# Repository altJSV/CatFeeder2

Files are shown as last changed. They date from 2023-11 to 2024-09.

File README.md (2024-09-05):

# CatFeeder 2
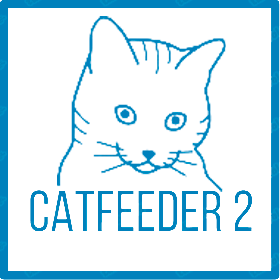
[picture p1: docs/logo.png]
Лого


Полная переработка проекта [CatFeeder](https://github.com/altJSV/CatFeeder) под ESP32.

## Оглавление
* [1. Особенности проекта](#Особенности-проекта)
*  [1.1. Отличия от CatFeeder](#Отличия-от-CatFeeder)
* [2. Сборка проекта](#Сборка-проекта)
*  [2.1. Необходимые компоненты](#Необходимые-компоненты)
*  [2.2. Сборка на макетной плате](#Сборка-на-макетной-плате)
*  [2.3. Сборка основного модуля управления](#Сборка-основного-модуля-управления)
*  [2.4. Подключение шагового двигателя](#Подключение-шагового-двигателя)
*   [2.4.1. Подключение драйвера MX1508](#Подключение-драйвера-MX1508)
*   [2.4.2. Подключение драйвера A4988](#Подключение-драйвера-A4988)
*  [2.5. Подключение весов](#Подключение-весов)
* [3. Прошивка](#Прошивка)
*  [3.1. Сборка из исходников](#Сборка-из-исходников)
*  [3.1.1. Необходимые библиотеки](#Необходимые-библиотеки)
*  [3.1.2. Особенности использования библиотек](#Особенности-использования-библиотек)
*  [3.2. Прошивка бинарных файлов](#Прошивка-бинарных-файлов)
* [4. Сборка-корпуса](#Сборка-корпуса)
* [4.1. Основная часть](#Основная-часть)
*  [4.2. Шнек](#Шнек)
*  [4.3. Миска](#Миска)
*  [4.4. Крышка с бункером для корма](#Крышка-с-бункером-для-корма)
*  [4.5. Регулируемые стойки](#Регулируемые-стойки)
* [5. Особенности использования](#Особенности-использования)
* [5.1. Первый запуск](#Первый-запуск)
*  [5.2. Управление с сенсорного экрана](#Управление-с-сенсорного-экрана)
*  [5.3. Веб интерфейс](#Веб-интерфейс)
*  [5.4. Настройка весов](#Настройка-весов)
*  [5.5. Управление через Telegram](#Управление-через-Telegram)
*  [5.6. Управление по MQTT](#Управление-по-MQTT)

## Особенности проекта
* Цветной TFT экран с сенсорным управлением
* Часы с синхронизацией времени по NTP протоколу
* Отображение температуры и влажности в помещении
* Настройки размера порции и времени кормления с 4 независимыми будильниками
* Точная настройка размера порции с помощью цифровых весов
* Калибровка цифровых весов в зависимости от температуры в помещении
* Проверка наличия корма в бункере и отслеживание забивания подающего лотка
* Уведомления и настройка некоторых параметров в Telegram
* OTA обновление прошивки как через веб интерфейс, так и через Телеграм бота
* Управление по MQTT протколу для интеграции в систему умного дома
* Веб интерфейс
* Сохранение и запись настроек в файлы конфигурации

### Отличия от CatFeeder
* Кормушка построена на базе ESP32, что позволяет существенно расширить ее функционал.
* Для управления используется цветной сенсорный дисплей ILI9341.
* Интерфейс реализован с помощью библиотеки LVGL.
* Все управление и настройки теперь осуществляется с помощью сенсорного экрана, что намного повышает удобство работы.
* Также был полностью переработан веб интерфейс и добавлено управление через телеграмм бота.
* Полностью переписано OTA обновление прошивки
* Работа через MQTT пока изменениям не подвергалась
* Все основные модули распаяны на макетной плате с колодками, для легкой замены.
* Шаговый двигатель теперь используется NEMA 17HS4023. По сравнению с предыдущим вариантом он более компактный и занимает гораздо меньше в корпусе. Мощность у него, конечно поменьше, но со своей задачей вращения шнека он полностью справляется.
* Полностью был переделан корпус. Как мне кажется, он стал более симпатичным и, надеюсь, поможет избавиться от проблемы застревания корма в подающем лотке.
* Также была полностью изменена логика выдачи корма. Теперь это не абстрактные цифры, а вполне конкретный вес в граммах. Для этого в корпус были интегрированы цифровые весы. Это позволяет не только точно отслеживать количество выдаваемого корма, но и своевременно реагировать на различные внештатные ситуации. Например "холостой ход двигателя" из-за застревания или окончания корма. Или же наоборот, подача корма в переполненную миску.

## Сборка проекта

### Необходимые компоненты
Для сборки проекта вам понадобятся следующие компоненты:
* Любая отладочная плата на базе ESP32. Я использовал [ESP32 WROOM 38 PIN](https://aliexpress.ru/item/1005004697343896.html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)
* Драйвер мотора MX1508. Например [такой](https://aliexpress.ru/item/1005001636421978.html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) или [драйвер шагового двигателя A4988](https://www.ozon.ru/product/a4988-stepper-motor-driver-with-ext-board-drayver-shagovogo-dvigatelya-s-platoy-rasshireniya-688838720/)
* [Повышающий преобразователь напряжения MT3608](https://www.ozon.ru/product/povyshayushchiy-preobrazovatel-napryazheniya-dc-dc-gsmin-mt3608-2a-vhod-2-24v-vyhod-5-28v-siniy-799440534/) - только при использовании драйвера A4988
* Шаговый двигатель [NEMA17 17HS4023](https://aliexpress.ru/item/10000232580902.html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)
* Сенсорный дисплей [ILI9341 2.8'](https://aliexpress.ru/item/4000219159401.html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) с разрешением 320x240 и драйвером тача XPT2046
* [Тензодатчик 5кг + драйвер HX711](https://aliexpress.ru/item/33046037411.html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)
* Набор проводов для соединений
* [Макетная плата 50х70 мм](https://aliexpress.ru/item/32945724064.html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)
* [Несколько разъемов hx2.54](https://aliexpress.ru/item/1005001479020815.html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) или похожих для подключения проводов
* [2 безголовых винта M3x2mm](https://aliexpress.ru/item/1005005451331078.html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) 
* [Модуль DHT22](https://aliexpress.ru/item/33037061522.html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)
* Качественный блок питания 5В 3А. Например [такой](https://www.ozon.ru/product/blok-pitaniya-5v-3a-micro-usb-dlya-raspberry-pi-3-i-pi-2-novaya-plata-422415562/) 
* Пластиковый квадратный пищевой контейнер с шириной основания 96 мм. Например [такой](https://www.ozon.ru/product/konteyner-vakuumnyy-dlya-edy-dd-style-hranenie-1200-ml-1-sht-994520444/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)

Далее, в соответствии со схемой, подключаем все компоненты.

### Сборка на макетной плате
Для сборки использовалась макетная плата 50х70 мм. Ниже описание процесса сборки с фото.
Для удобства сборки проект состоит из нескольких модулей.
* Основной модуль управления. На нем находится плата ESP32, Micro USB разъем для питания и разъемы для подключения остальных модулей.
* Модуль управления шаговым двигателем. Представляет собой плату MX1508 с распаянными колодками для подключения.
* Модуль контроллера весов. Представляет собой плату HX711 с распаянными колодками для подключения тензодатчика и ESP32.

#### Сборка основного модуля управления
На макетной плате распаиваются колодки для подключения ESP32 и разъемы hx2.54 для подключения дополнительных модулей. Также припаивается и Micro USB разъем для подключения питания.
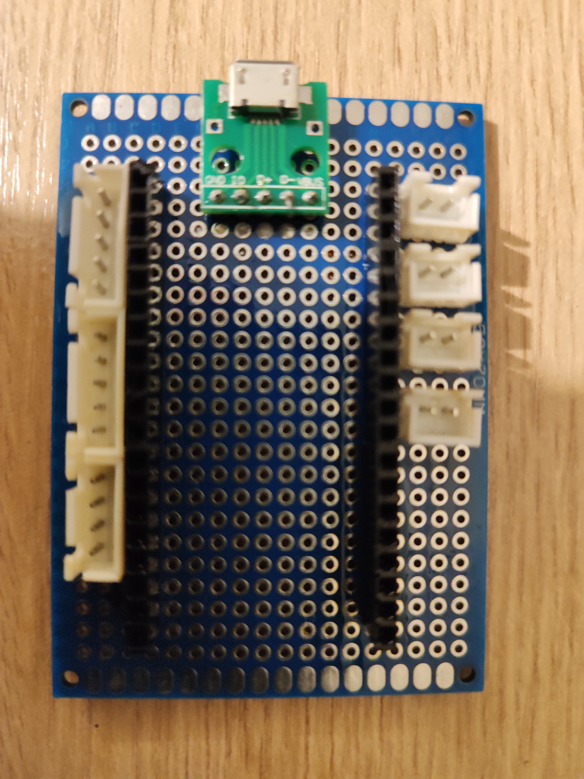
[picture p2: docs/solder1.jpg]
Распайка разъемов


С подключенным ESP32 управляющая плата выглядит следующим образом.
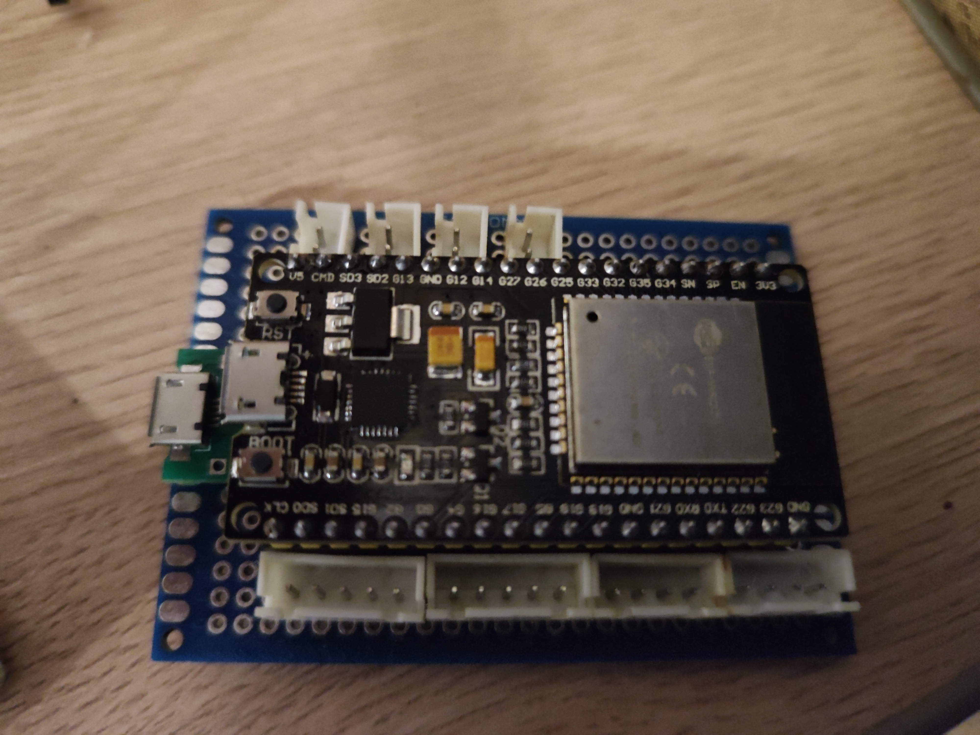
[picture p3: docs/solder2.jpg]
Подключение ESP32


С обратной стороны платы, соединяются проводами контакты разъема ESP32 с разъемами на плате. Провода использовал из обрезка витой пары. Ниже одно из ранних фото процесса. Еще не все контакты распаяны.
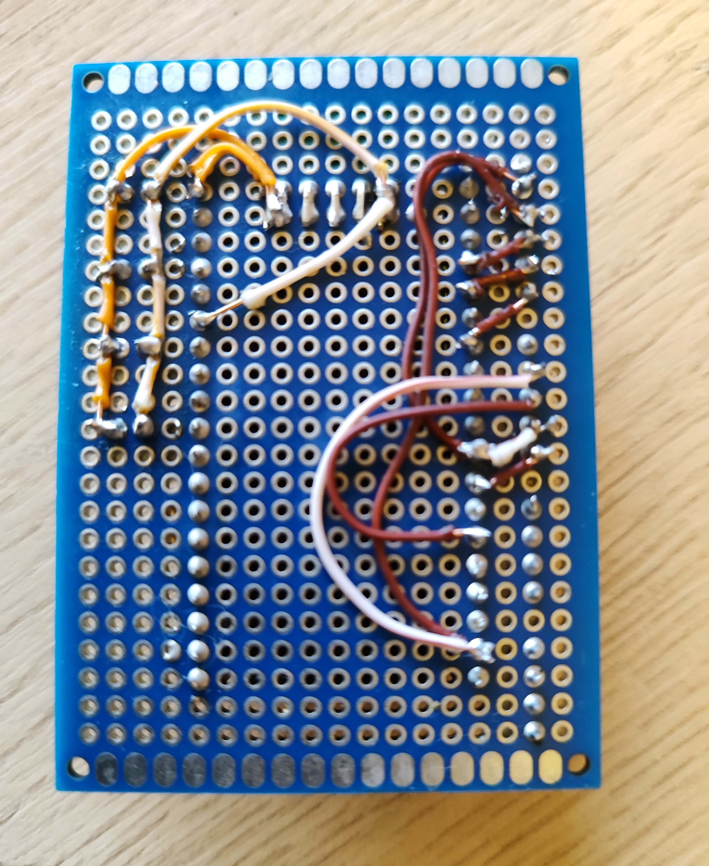
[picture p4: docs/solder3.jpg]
Вид сзади


Для удобства, при пайке, можете сверяться со схемой ниже
Схема пайки

Модуль DHT22 распаян прямо на плате.
Шлейфы, для подключения дополнительных модулей, делал из той же витой пары. На фото ниже шлейф дисплея.
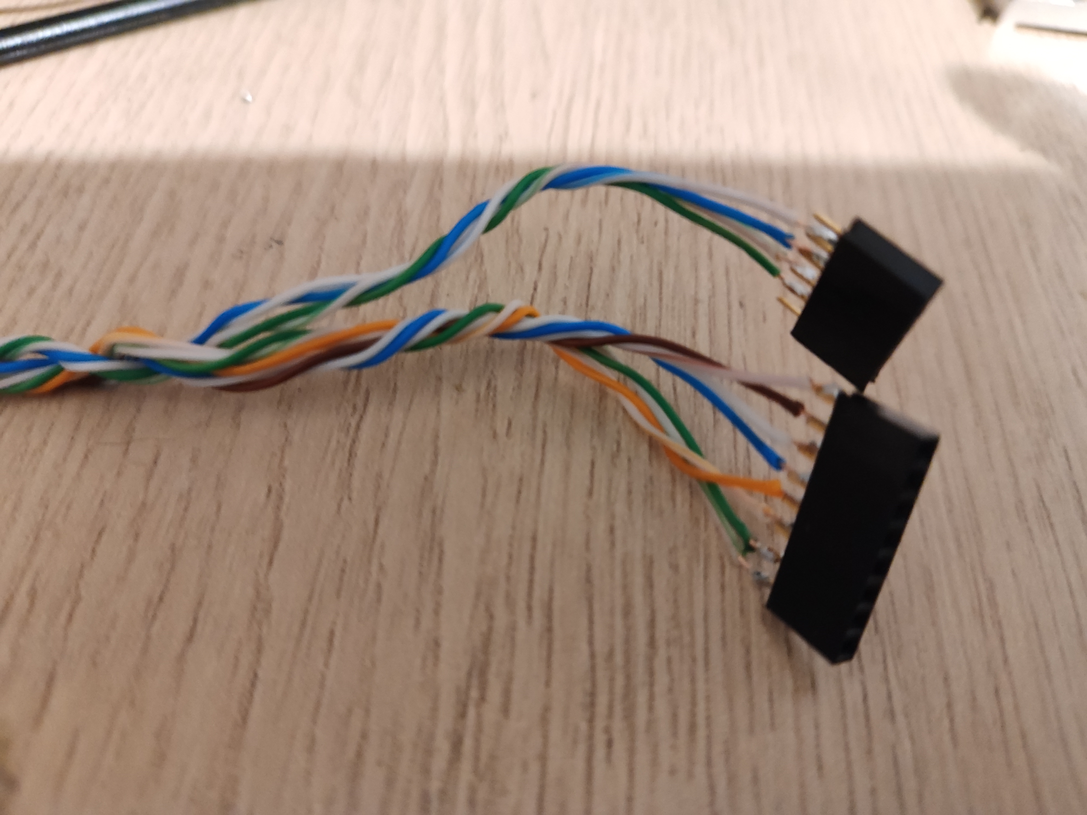
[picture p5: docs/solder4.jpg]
Шлейф дисплея


После пайки платы, обязательно прозвоните все контакты мультиметром и изолируйте все места пайки. Паяльной маской, термоклеем или тем, что у вас есть под рукой.
Два разъема питания из четырех, пока никак не задействованы и были оставлены для возможных будущих модификаций.

### Подключение шагового двигателя

Для привода шнека кормушки в движение используется шаговый двигаетель Nema17 17HS4023. Крутящего момента хватает, но лучше все же использовать Nema17 42HS34 или подобный.

Потребляемый ток при максимальной нагрузке может достигать до 1.5А, поэтому необходимо подключение качественного блока питания. Я использовал блок питания 5В 3А. 

Для управления шаговым двигателем используется специальная плата-драйвер. Прошивка поддерживает следующие типы драйверов:
* MX1508 - самый дешевый, но вместе с тем самый ненадежный вариант. Его главное достоинство - дешевизна. Также драйвер и мотор можно питать от 5 вольт. Из недостатков мотор шумит, иногда довольно ощутимо греется, снижен курутящий момент
* А4988 - чуть более дорогой вариант, но гораздо более лучший по всем параметрам. Крутящий момент максимальный, мотор практически не греется, возможна точная настройка шагов, регулировка опорного напряжения двигателя и многое другое. Из недостатков это необходимость установки дополнительного повышающего трансформатора на 9 вольт для питания мотора, гораздо более высокая цена. И двигатель при работе все еще ощутимо шумит. Как вариант можно установить драйвер TMC2208. С ним мотор работает ощутимо тише, но и драйвер сильно дороже.

Выбор способа подключения драйвера осуществляется в прошивке в файле CatFeeder2.ino заменой значения дефайна:
```
//Выбор типа драйвера
#define STEPDRVTYPE 1 //0-MX1508,  1 - A4988
```
По умолчанию используется драйвер А4988.

#### Подключение драйвера MX1508
Для подключения драйвера MX1508 просто припаиваем к нему несколько разъемов JST 2.0. HX2.54, к сожалению, не подойдет из-за раздличий в расстоянии между монтажными отверстиями. Общий вид платы на фото:

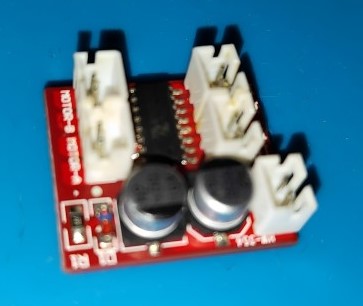
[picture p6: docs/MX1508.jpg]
MX1508


Общая схема подключения к драйверу и микроконтроллеру на схеме ниже:
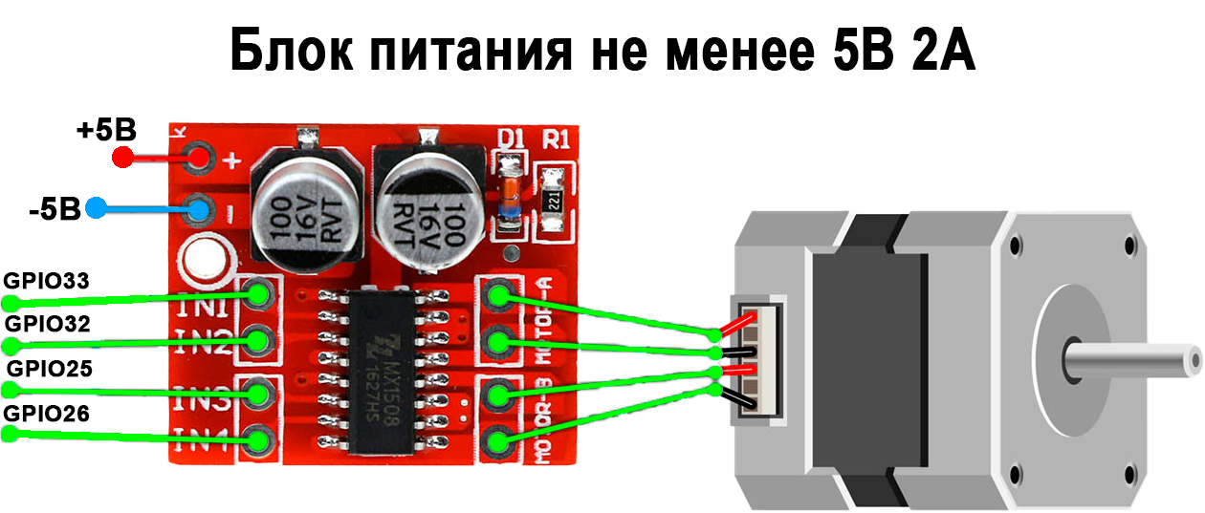
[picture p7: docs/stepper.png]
Подключение шагового двигателя


Также следует учитывать, что при использовании этого драйвера, шаговый двигатель очень чувствителен к силе тока подаваемой на обмотки. При использовании 17HS4401 ток, выдаваемый драйвером (около 1.5А на обмотку), вполне достаточен. Но для 17HS4023 это все же многовато. Двигатель может работать неправильно. Пропуски шагов, нагрев и все в таком духе. Помогает установка резисторов 3.3 Ома в разрыв проводов идущих к двигателю. Номинал во многом еще зависит от типа и толщины используемых проводов, но на комплектных проводах шаговика этот номинал вполне достаточен.
Как вариант можно использовать 17HS08-1004S. По размерам он немного меньше, но крутящий момент почти такой же. И номинальный ток несколько выше, так что должно работать и без резисторов.

#### Подключение драйвера A4988

Для более удобного подключения, рекомендую использовать плату расширения. Общий вид платы и драйвера на фото ниже:
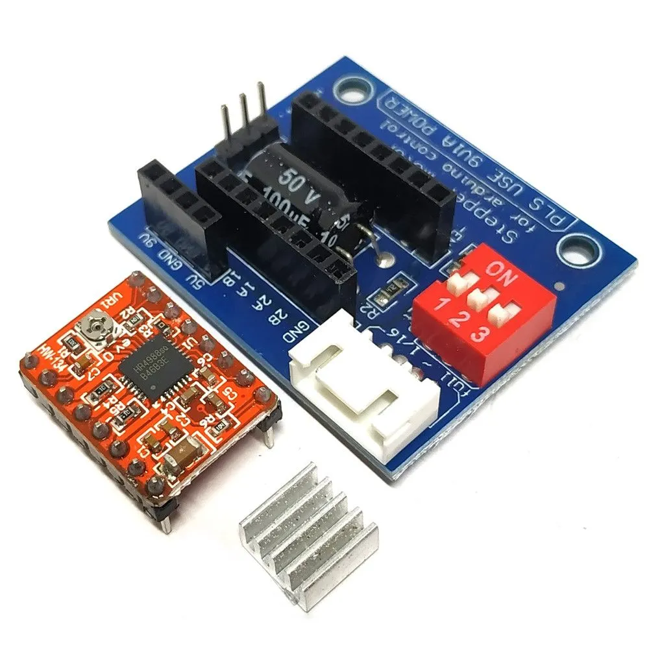
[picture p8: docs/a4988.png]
A4988


Диаграмма подключения на схеме ниже:
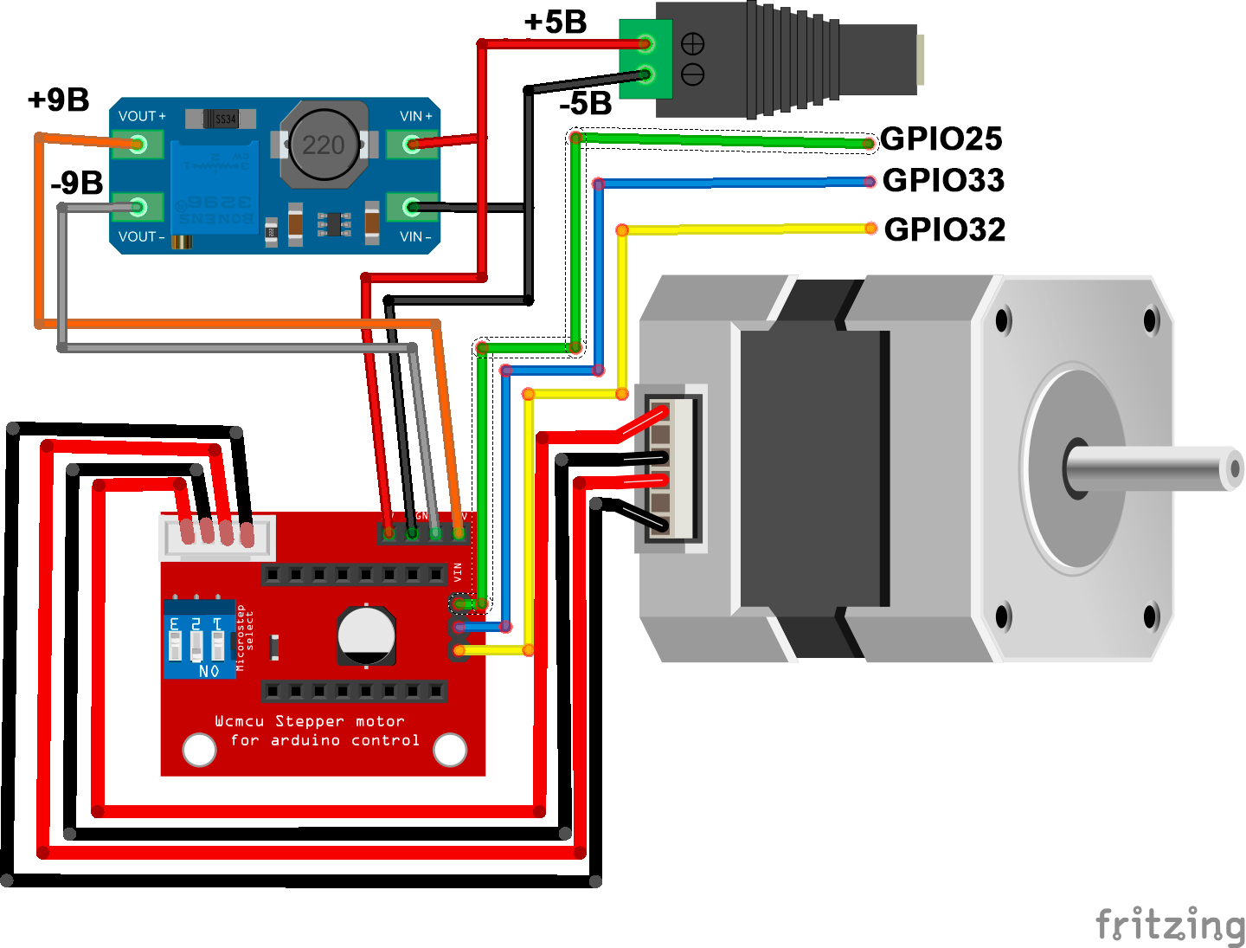
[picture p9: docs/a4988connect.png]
A4988connection


Значение всех переключателей на плате расширения установить в положение OFF. Питание драйвера 5 вольт - можно взять с разъема на основной плате. Питание двигателя, также берется из разъема основной платы 5в и подключается через MT3608, установленным на 9 вольт.
Пины на плате расширения подключать к ESP32 по следующей схеме:
* **Step - GPIO35**
* **Dir - GPIO36**
* **EN - GPIO25**

Также при использовании шагового двигателя 17HS4023, необходимо установить опорное напряжение 0.7В с помощью подстроечного резистора на плате драйвера. Для этого включите устройство в сеть и установите плюсовой щуп мультиметра прямо на винт подстроечного резистора, минусовой на массу, и измерьте напряжение. Далее, с помощью мелкой крестовой отвертки, немного покрутите винт резистора до установки требуемого напряжения. Для 17HS4023 опорное напряжение должно быть около 1.5 вольта.

### Подключение весов
Подключение тензодатчика осуществляется через модуль HX711 по следующей схеме:
Подключение тензодатчика

## Прошивка
Установка прошивки возможна двумя способами. С помощью сборки из исходников и с помощью предварительно скомпиллированных бинарных файлов.

### Сборка из исходников
Сборка и установка прошивки осуществляется в среде разработки Arduino IDE

#### Необходимые библиотеки
Для сборки проекта вам необходимо установить дополнительные библиотеки для Arduino IDE:
* LVGL - 8.3.10
* TFT_eSPI - 2.5.0 и выше
* GyverNTP - 1.3.1
* GyverTimer - 3.2
* PubSubClient от Nick O'Leary - 2.8
* ArduinoJSON - 6.21.3
* FastBot - 2.25
* GyverHX711 - 1.2

Также необходимо установить следующие настройки компилятора:
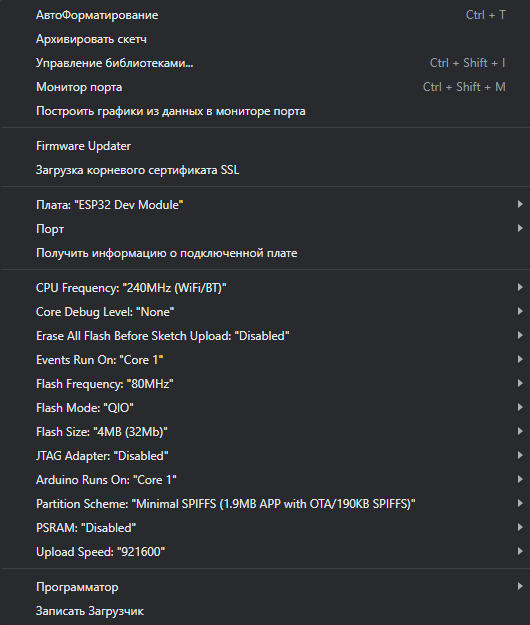
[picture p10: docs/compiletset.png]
Настройки компилятора


#### Особенности использования библиотек
В проекте используется стандартная библиотека **LVGL - 8.3.10**, но с некоторыми модификациями исходного кода. В папке проекта **extra** находится модифицированная версия библиотеки. Просто скопируйте содержимое архива **lvgl.7z** в папку с библиотеками Arduino, при необходимости подтвердив замену файлов.
Также в папке extra находится конфигурационный файл для библиотеки **TFT_eSPI** - *User_Setup.h*. Скопируйте его в папку **TFT_eSPI**, заменив исходный файл при необходимости.

### Прошивка бинарных файлов
Для прошивки вам понадобится официальная программа от Espresif [Flash Download Tools](https://www.espressif.com/sites/default/files/tools/flash_download_tool_3.9.5.zip).
После запуска программы, на первом экране установите следующие настройки:

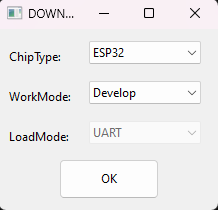
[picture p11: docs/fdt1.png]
Настройки Flash Download Tools


На втором экране укажите путь к бинарным файлам из архива проекта и их адреса во флеш памяти. Скорость SPI - *40Mhz*, режим записи - *DIO*, установить флажок -  *DoNotChgBin*. Для удобства можете сверяться со скриншотом ниже:

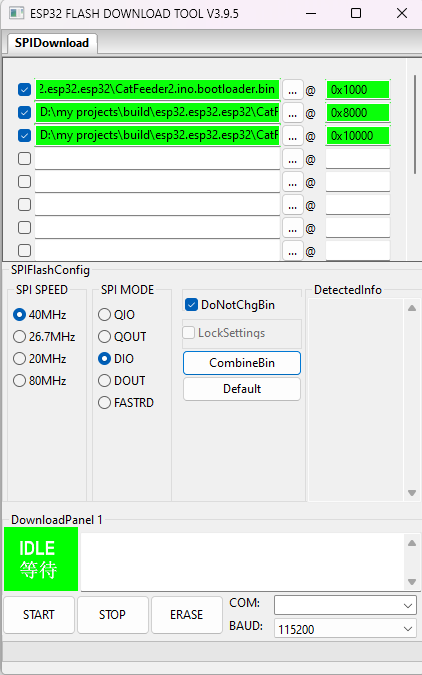
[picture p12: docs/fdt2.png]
Настройки Flash Download Tools 2


Значение COM выбирайте исходя из того, какой виртуальны порт присвоил драйвер USB-TTL вашему устройству.
Теперь необходимо полностью очистить соедержимое флеш памяти ESP32. Нажмите на кнопку *ERASE* и подключите ваш  ESP32 к компьютеру по USB с зажатой кнопкой BOOT.
Через некоторое время прогресс бар внизу окна прошивальщика начнет заполняться. После окончания процесса вам будет выведено уведомление **Finish**
Теперь можно установить и саму прошивку. Нажмите кнопку START и повторите весь процесс с подключением ESP32 по USB к компьютеру с зажатой кнопкой BOOT на модуле.
После полного заполнения шкалы прогресса и вывода уведомления **Finish** можно закрыть прошивальщик и отключить ESP32 от компьютера.

## Сборка корпуса
Все основновные части корпуса распечатаны на 3Д принтере. Модели для печати расположены в папке **3dmodel**. Также в ней расположены исходники для Fusion360.

Корпус состоит из 5 частей.
1. Основная часть
2. Шнек
3. Миска
4. Крышка с бункером для корма
5. Регулируемые стойки

Общий рендер корпуса с установленными компонентами на скриншоте ниже:
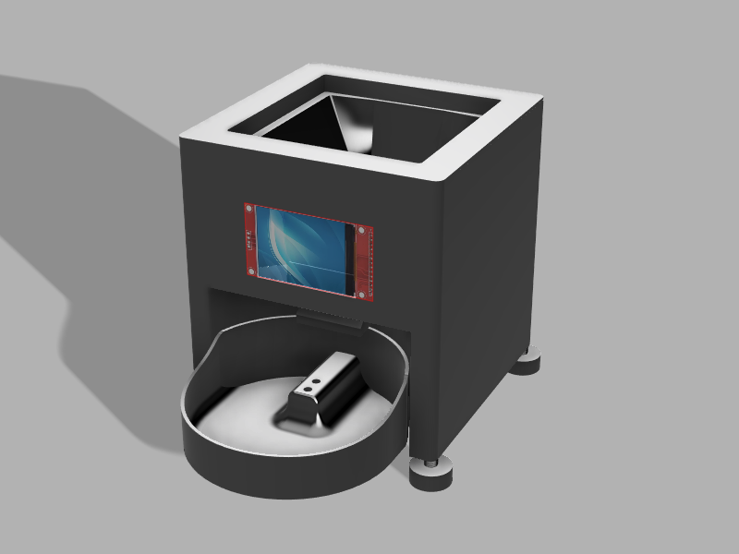
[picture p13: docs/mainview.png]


### Основная часть
Служит для размещения всех компонентов устройства. Схема расположения электронных компонентов в корпусе на рендере ниже. 
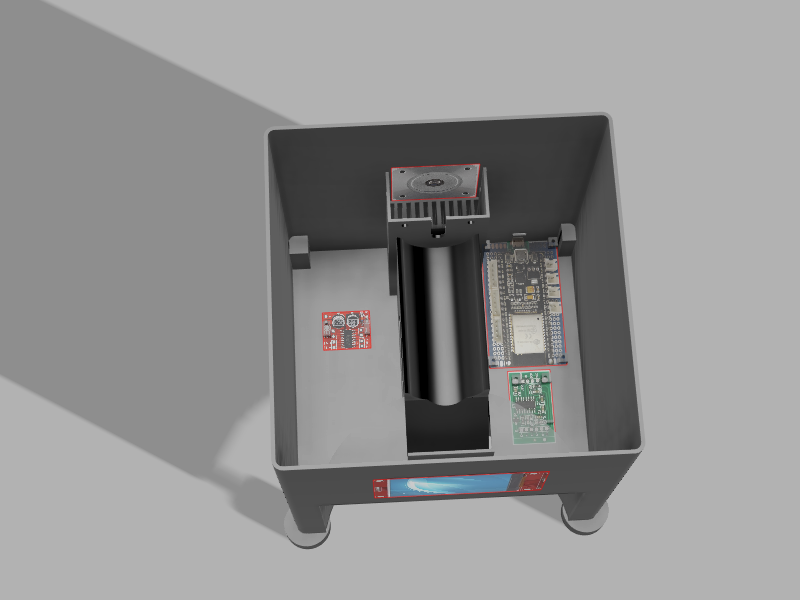
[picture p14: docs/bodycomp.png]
Крепление электронных компонентов


Большая часть всех компонентов крепится винтами m3x3мм. Шаговый двигатель крепится двумя винтами М4x8мм.
**Основные параметры печати:**
* Пластик: PETG
* Высота слоя: 0.2 мм
* Температура сопла: 230
* Температура стола: 75
* Плотность заполнения 20%
* Поддержки: везде

### Шнек
Служит для подачи корма в миску. Одевается на вал шагового двигателя с небольшим натягом. 
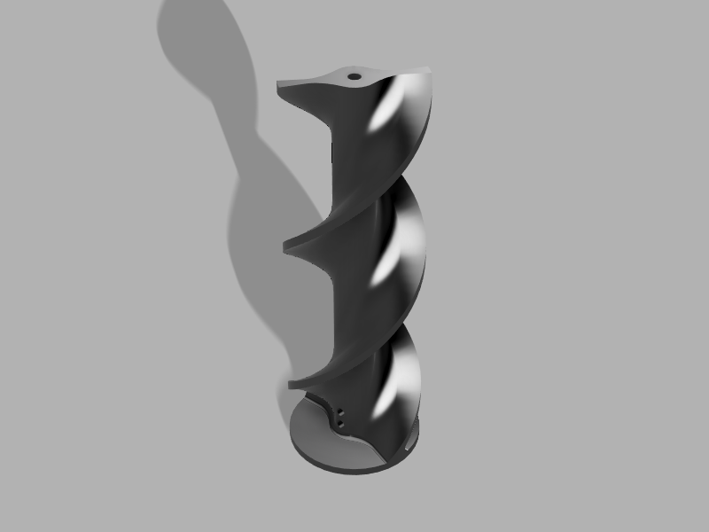
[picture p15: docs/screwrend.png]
Шнек


Для дополнительной фиксации используется 2 безголовых винта M3x2мм.
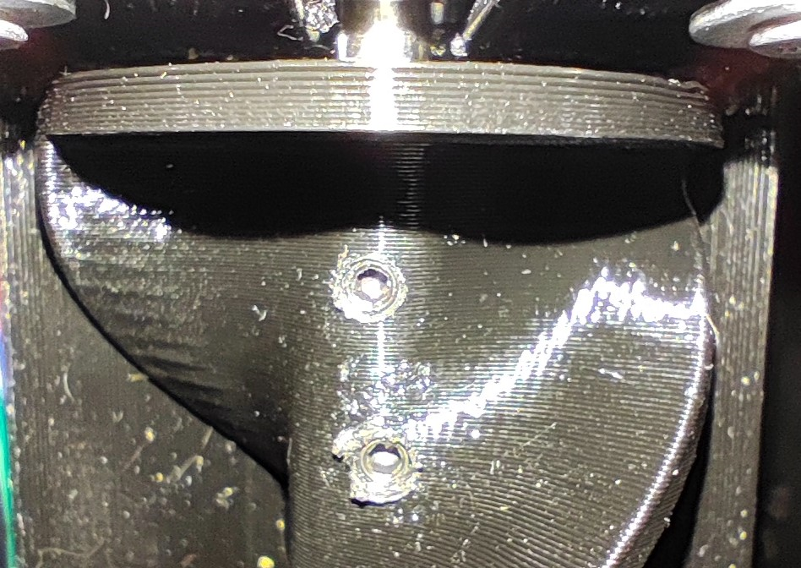
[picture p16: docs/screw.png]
Крепление шнека


**Основные параметры печати:**
* Пластик: PETG
* Высота слоя: 0.1 мм
* Температура сопла: 230
* Температура стола: 75
* Плотность заполнения 100%
* Поддержки: нет

### Миска
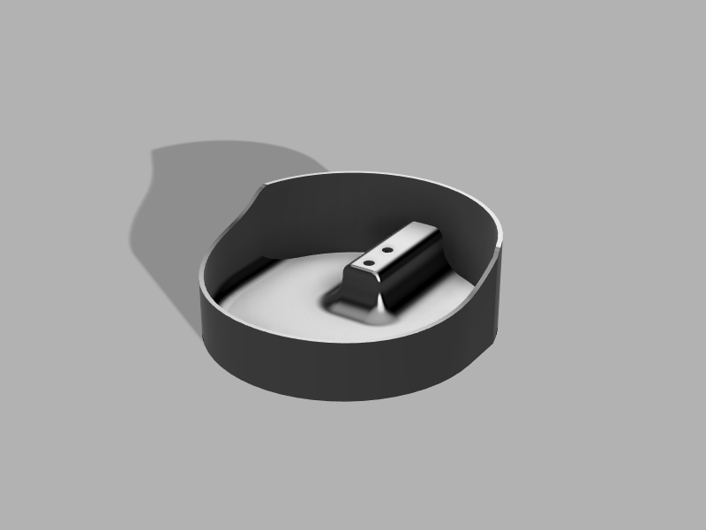
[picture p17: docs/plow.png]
Миска


Соединяется с тензодатчиком с помощью 2 винтов М4x16. Затем в сборе через технологическое отверстие вставляется в корпус. После чего другая сторона тензодатчика фиксируется двумя винтами М5х16, вставленными через отверстия внизу корпуса.
**Основные параметры печати:**
* Пластик: PETG
* Высота слоя: 0.2 мм
* Температура сопла: 230
* Температура стола: 75
* Плотность заполнения 20%
* Поддержки: от стола

### Крышка с бункером для корма
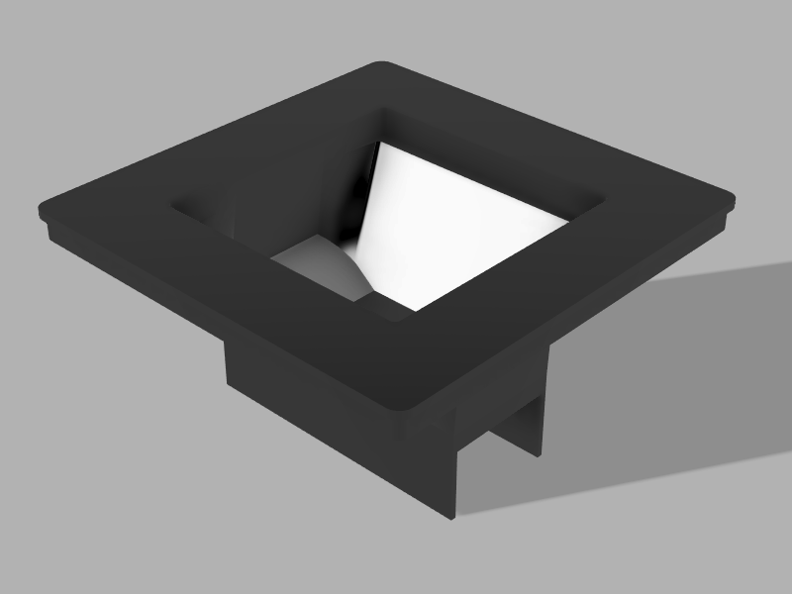
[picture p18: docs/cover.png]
Крышка


На ней размещен бункер для корма. Также обеспечивает доставку корма к подающему шнеку. В качестве бункера для корма используется квадратный пищевой контейнер из оргстекла с основанием 96 мм из списка компонентов. В нижней его части выерезается отверстие для подачи корма. Для установки в крышку, в ней предусмотрено отверстие с упорами по углам. Потом контейнер дополнительно фиксируется термоклеем по углам.
Для установки крышки в корпус на ней предумострены направляющиев в врехней части. Дополнительная фиксация не требуется.
**Основные параметры печати:**
* Пластик: PETG
* Высота слоя: 0.2 мм
* Температура сопла: 230
* Температура стола: 75
* Плотность заполнения 20%
* Поддержки: от стола

### Регулируемые стойки
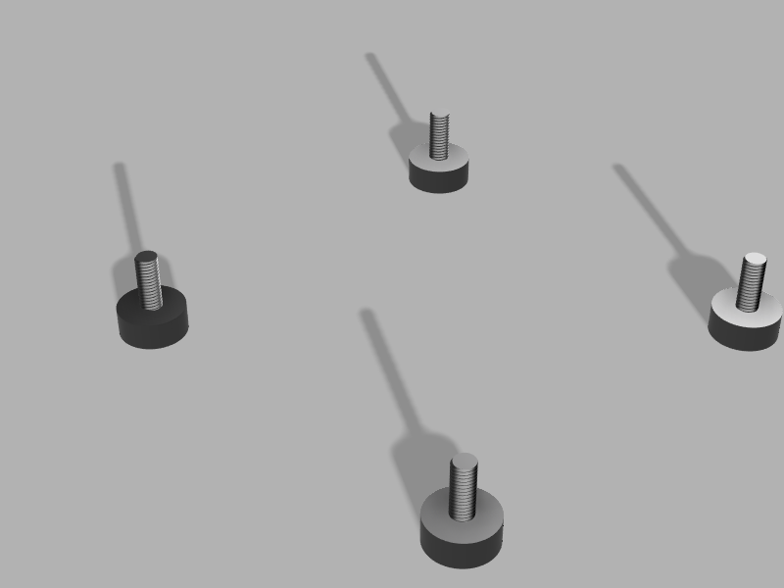
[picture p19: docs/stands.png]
Стойки


Представляют собой 4 ножки с резьбой М8х1.25 для регулировки кормушки по высоте и выравнивания ее на плоскости.В нижней части корпуса под них предусмотрены соответствующие отверстия с резьбой.
**Основные параметры печати:**
* Пластик: PETG
* Высота слоя: 0.1 мм
* Температура сопла: 230
* Температура стола: 75
* Плотность заполнения 100%
* Поддержки: нет

Фото первого рабочего прототипа представлено на фото ниже. На нем еще присутствуют некоторые недостатки, которые были исправлены в финальной версии.
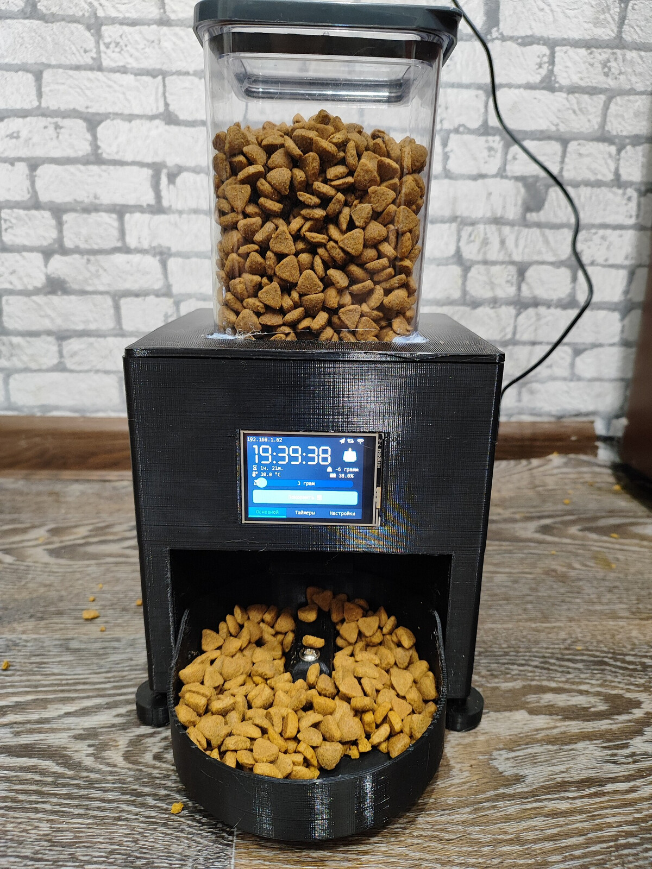
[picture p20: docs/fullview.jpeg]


## Особенности использования
Данный раздел посвящен особенностям использования Cat Feeder 2. 

### Первый запуск
После сборки и загрузки прошивки, при первом запуске устройства, происходит процесс инициализации. Условно его можно разделить на несколько этапов:

1. Форматирование файловой системы и создание конфигурационных файлов;
2. Калибровка сенсорного экрана;
3. Настройка подключения к WiFi;
4. Запуск всех основных сервисов и настройка параметров работы;
5. Переход в рабочий режим;

Разберем каждый из этапов более подробно. На первом этапе проверяется наличие раздела ФС для хранения конфигурационных файлов. Если раздел обнаружен, то производится его форматирование в файловую систему SPIFFS и устройство перезагружается.

На следующем этапе проверяется наличие в файловой системе устройства файла TouchCalData, с данными калибровки сенсорного дисплея. При его отсутсвии или чтении некорректных значений, инициализируется процесс калибровки экрана. В разных углах дисплея последовательно будут появляться стрелки. Вам необходимо касаться стилусом острия каждой из них. Как только процесс будет закончен, в файловой системе создается файл TouchCalData, с данными калибровки сенсорного дисплея, и устройство перезагружается.

Далее происходит настройка подключения к WiFi. Проверяется наличие учетных данных для подключения к сети в специальном разделе памяти устройства. Если они отсутсвуют, то создается точка доступа "CatFeeder2", к которой вам необходимо подключится по Wifi.На экране при этом не будет отображено никакой информации. После подключения к точке доступа по WiFi, перейдите в браузере по адресу http://192.168.4.1 и, в открывшемся веб интерфейсе, введите ваши учетные данные. После нажатия кнопи **Save**, устройство в очередной раз перезагрузится.

Далее, при следующем запуске, производится попытка запуска всех основных сервисов, таких как: веб интерфейс, mqtt клиент, телеграм бот, служба синхронизации времени, сенсорный интерфейс экрана. Если вы собирали прошивку из исходников, то учетные данные для mqtt и telegram, автоматически загрузятся из конфигурационного файла secrets.h. Если же вы загружали прошивку через предварительно скомпилированный бинарный файл, то вам необходимо настроить эти параметры через веб или сенсорный интерфейс. Также необходимо откалибровать платформу весов, настроить яркость дисплея, таймеры, шаги двигателя и прочие параметры. Все изменения автоматически сохраняются в конфигурационном файле config.json в файловой системе устройства. Далее они будут применяться при каждом перезапуске.

И, наконец, кормушка переходит в рабочий режим. Можно попробовать выдать порцию корма, нажав кнопку **Покормить** на главном экране. Если все прошло успешно, то устройство готово к работе и далее будет действовать в атоматическом режиме.

### Управление с сенсорного экрана
Сенсорный интерфейс управления устройством разделен на 3 основные вкладки:
* Главная
* Вкладка будильников
* Вкладка настроек
Перемещение по ним осуществляется либо тапом по имени вкладки в нижней части экрана, либо свайпами влево или вправо.
Фото главного экрана представлено на фото ниже:
MainScreen

В верхней части экрана расположена статусная строка. В ней отображаются: IP адрес, присвоенный устройству, а также индикаторы состояния подключения к телеграм боту, mqtt брокеру и сети wifi.
Ниже расположена информационная панель с отображением текущего времени, полученного c ntp сервера, время оставшееся до начала кормления, температура и влажность воздуха в помещении.
Еще ниже расположен слайдер размера порции. Он может принимать значение от 1 до 60 грамм. Под ним находится кнопка для немедленной выдачи установленного колличества корма. Тапом по иконке шагового мотора, справа от часов, осуществляется переход в окно настроек шагового двигателя.
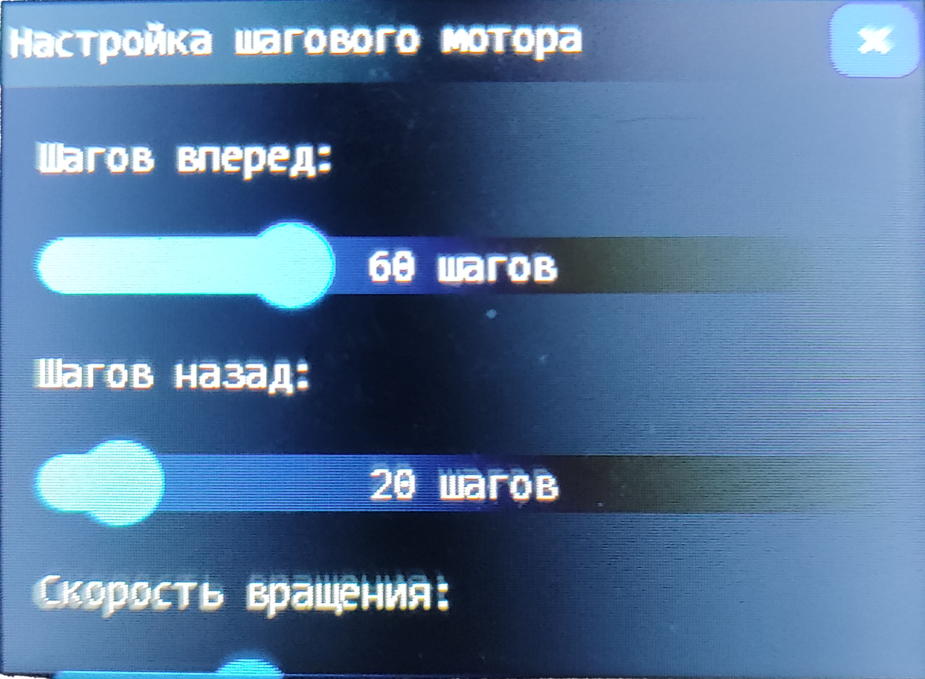
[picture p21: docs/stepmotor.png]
Stepmotor


В данном окне производится тонкая настройка двигателя.
Для предотвращения застревания корма, двигатель вращает шнек на несколько шагов вперед, потом немного назад. В окне настраивается колличество этих шагов, а также скорость вращения двигателя. Полный оборот двигатель совершает за 200 шагов. Поэтому слайдеры работают в этом пределе. Также в нижней части окна, расположена кнопка тестового запуска двигателя для проверки настроек.
Тапом по вкладке **Таймеры** можно перейти в меню настройки будильников.
alarms

Всего для редактирования доступны 4 будильника. В каждом из которых вы можете установить время срабатывания и колличество выдаваемого корма. Также вы можете включить или выключить любой из таймеров.
Тап по вкладке **Настройки** открывает доступ к различным параметрам устройства. Для удобства они разделены на несколько категорий.
В категории **Настройки дисплея** находится все что касается экрана устройства.
screenset

В частности здесь вы можете откалибровать сенсорную панель, настроить яркость подсветки и изменить тему оформления.
Светлая тема оформления представлена на фото ниже:
lighttheme

Следующая категория **Настройки времени**.
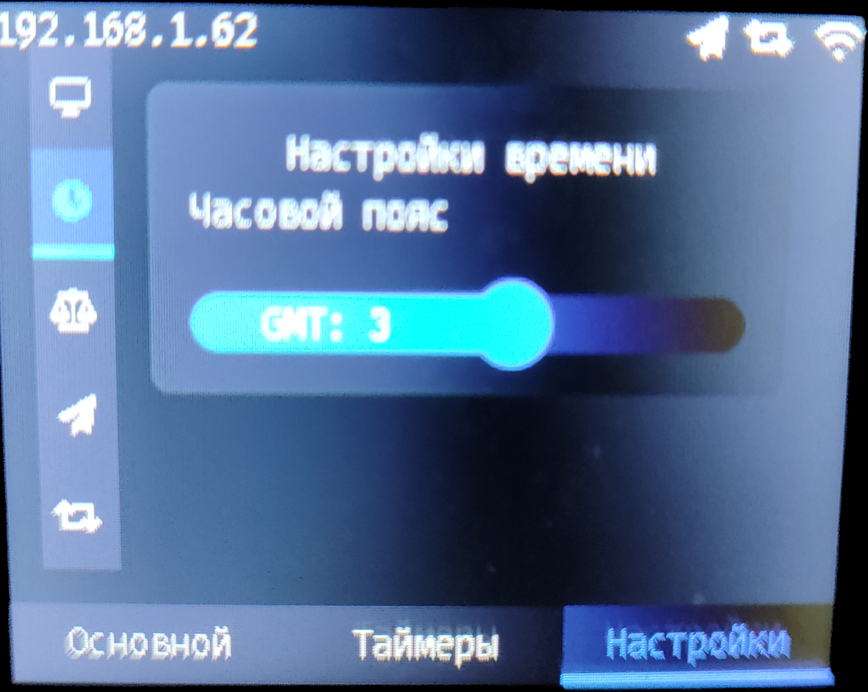
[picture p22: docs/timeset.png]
timeset


В ней пока присутствует лишт один параметр. Настройка часового пояса для синхронизации времени.
Далее идет **Калибровка весов**.
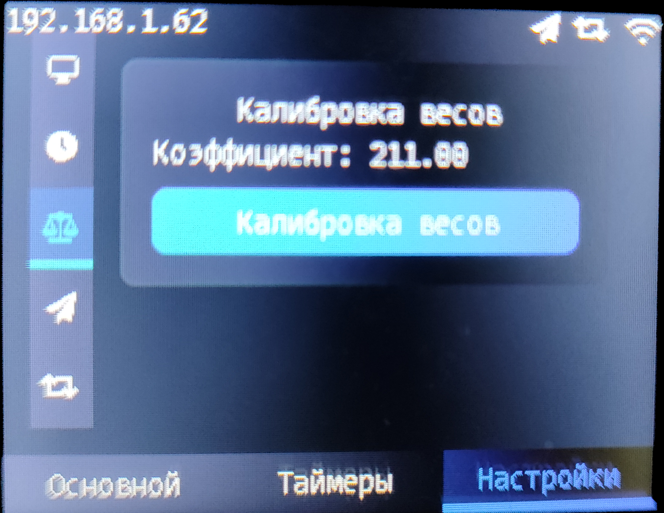
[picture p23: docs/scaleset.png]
scaleset


В ней можно выполнить калибровку весовой платформы. Подробнее об этом в главе [Настройка весов](#Настройка-весов).
Следующая категория **Настройки Telegram бота**.
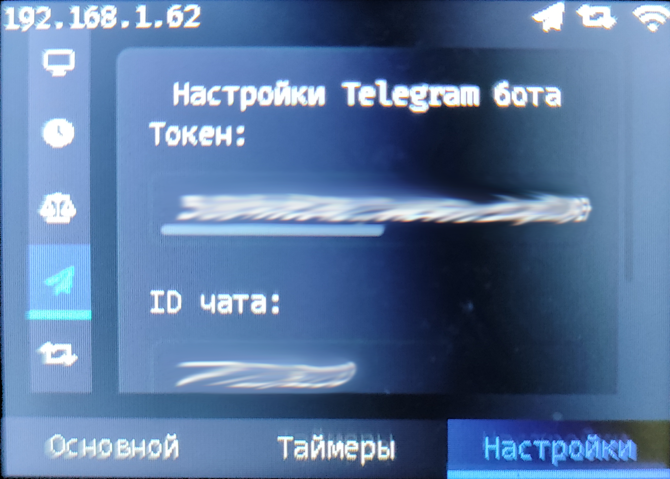
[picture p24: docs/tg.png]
tg


В ней вы можете включить или отключить использование бота и настроить различные параметры подключения.
И последняя категория **Настройки MQTT**.
mqtt

В ней устанавливаются различные параметры подключения к MQTT брокеру.

### Веб интерфейс
Для доступа к вебинтерфейсу кормушки просто введите в адресной строке браузера следующий текст: **https://catfeeder2.local**. Если по какой-либо причине данный способ не работает, то перейти в веб интерфейс можно введя IP адрес кормушки в адресную строку браузера. Узнать его можно посмотрев в левый верхний угол экрана устройства.
Общий вид веб интерфейса представлен на скриншоте ниже:

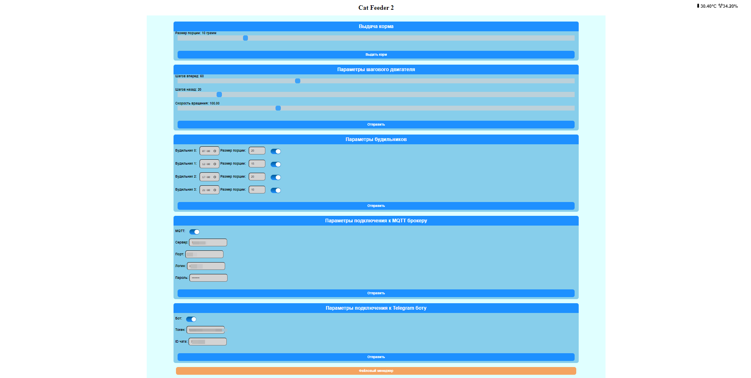
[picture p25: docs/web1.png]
Web1


На данном экране вы можете:
* Выдать порцию корма заданного веса;
* Настроить параметры шагового двигателя;
* Посмотреть и отредактировать все установленные будильники;
* Настроить параметры подключения к MQTT брокеру;
* Настроить параметры подключения к Telegram боту;
* Перейти на экран работы с файловой системой;

**Обратите внимание**, что значения всех параметров сохраняются только после нажатия кнопки **Отправить**!

При нажатии на кнопку **Файловый менеджер** откроется новый экран работы с файловой системой устройства.

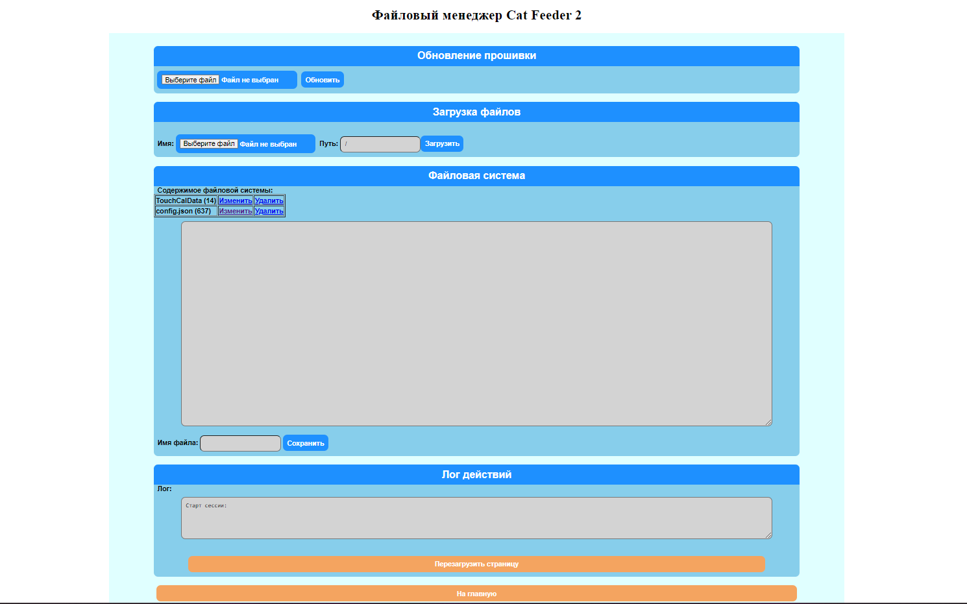
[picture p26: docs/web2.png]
Web2


На данном экране вы можете:
* Загрузить прошивку в устройство;
* Загрузить файл в файловую систему;
* Просмотреть содержимое памяти устройства и отредактировать/удалить файлы;
* Просмотреть лог работы устройства;
* Перезагрузить активную страницу;
* Вернуться на главную страницу;

### OTA обновление прошивки
Устройство поддерживает обновление прошивки "По воздуху". Для его выполнения зайдите в веб интерфейс устройства. В нижней части страницы нажмите на кнопку "**Файловый менеджер**".
OTA1

Далее в разделе Обновление прошивки с помощью кнопки **Выберите файл** укажите путь к файлу прошивки и нажмите **Обновить** для его загрузки в устройство.
OTA2.

Также поддерживается обновление прошивки и через Телеграм бота. Достаточно, лишь в диалоге с ним отправить ему скомпилированный бинарный файл.

### Настройка весов
Перед первым использованием весы кормушки необходимо откалибровать. Перед калибровкой желательно дать поработать кормушке 5-10 минут в дежурном режиме. Это связано с тем, что HX711, сразу после запуска выдает несколько завышенные показания. Из-за этого показатели веса на платформе постоянно плавают. Примерно минут через 5, все приходит в норму и выдаются примерно одинаковые данные. С чем это связано, я не знаю. Возможно брак конкретно моего модуля. 
Далее для калибровки подготовьте груз с заранее известным весом. После чего перейдите на вкладку **Настройки**.
Далее откройте раздел **Весы**. Вверху страницы находится информация о настроенном калибровочном коэффициенте. 
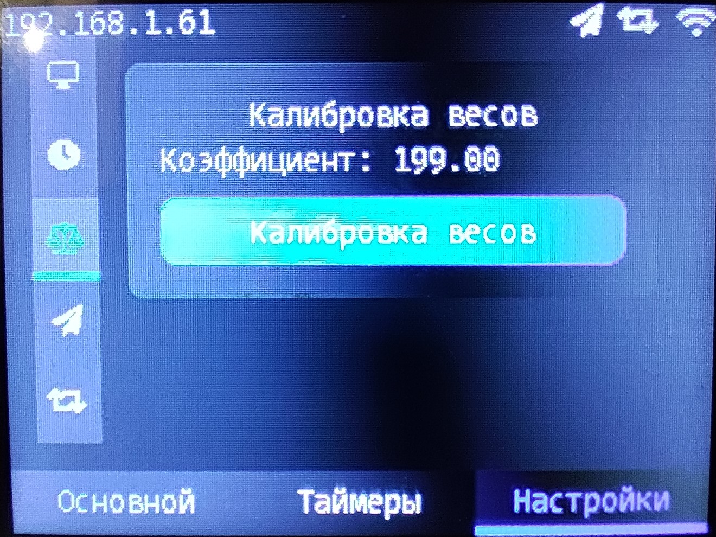
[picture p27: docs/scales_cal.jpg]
Калибровка весов 1


Нажмите кнопку **Калибровка весов**. 
Откроется новое окно.
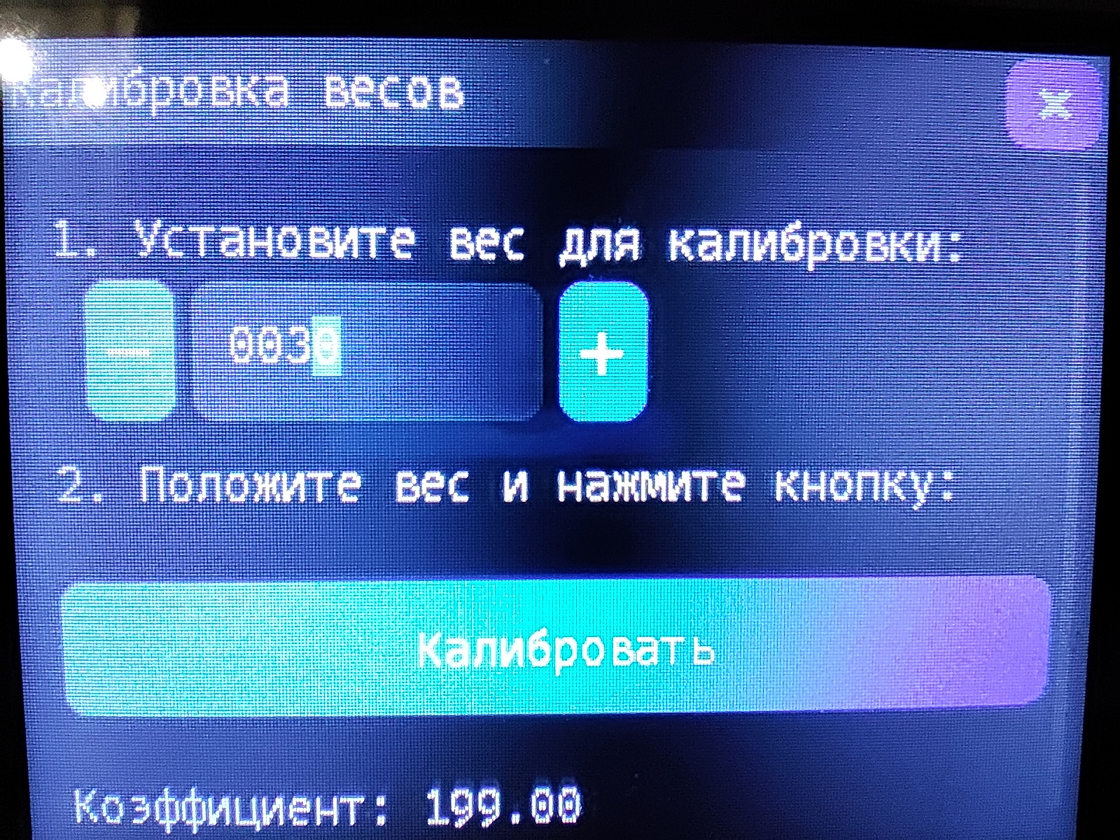
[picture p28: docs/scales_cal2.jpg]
Калибровка весов 2


В нем установите вес груза и положите его на платформу весов. После чего нажмите кнопку **Калибровать**. Новый коэффициент будет расчитан и отобразится в нижней части окна. 
При калибровке также запоминается значение текущей температуры в помещении. Далее значения полученные с весов будут корректироваться в зависимости от температуры в помещении.
Закройте окно, для сохранения изменений.

### Управление через Telegram
Для управления кормушкой через Telegram бота прежде всего необходимо его создать воспользовашись [инструкцией](https://projectalt.ru/publ/arduino_esp8266_i_esp32/programmirovanie/upravlenie_esp8266_cherez_telegram_bota/11-1-0-38) и получить API ключ и ваш ChatID.
Далее, если вы собираете прошивку из исходников, измените значения переменныйх *String bot_token = "1234567890" и String chatID = "chat"* в файле secrets.h на полученные вами учетные данные.
Если вы прошили устройство с помощью предварительно скомпилированных бинарных файлов, то данные параметры можно изменить на вкладке "Настройки" в разделе Telegram.
Если все настроено корректно, то кормушка  при старте отправляет боту сообщение: "Cat Feeder 2 готов к работе!".
Также поддерживается OTA обновление прошивки через бота. Достаточно в диалоге отправить ему через вложение скомпилированный бинарный файл с прошивкой.

#### Полный список управляющих команд
Команда без параметра включает или отключает функцию. С параметром - устанавливает значение или выполняет действие. 
* **/feed** - выдача одной порции корма. (Если указан параметр, то выдать определенное колличество 1-60 гр). Например **/feed 40**.
* **/info** - получение статусной информации о работе кормушки
* **/lastfeed** - время последнего кормления и размер порции
* **/temp** - температура и влажность
* **/mqtt** - включение/отключение MQTT
* **/brightlevel** - установить яркость подсветки экрана (параметр 0-255)
* **/daytime** - без параметра, включение и отключение снижения яркости экрана. Параметр вида hn:he установка дневного времени. hn-начало, he-конец
* **/restart** - перезагрузка устройства
* **/commandlist** - справка по командам

Следующие команды без параметра включают или отключают будильники. С параметром устанавливают его значение и сохраняют в память
Параметр вида **hh:mm** устанавливает время. Например, **/alarm0 11:20**. Параметр val размер порции в граммах. Например, **/alarm0 40**.
* **/alarm0** - Будильник 0
* **/alarm1** - Будильник  1
* **/alarm2** - Будильник  2
* **/alarm3** - Будильник  3

### Управление по MQTT
Для управления кормушкой по протоколу MQTT необходимо выполнить ряд настроек. В файле secrets.h изменить значения следующих переменных:

`String mqtt_server = "192.168.1.1"; //ip или http адрес
int mqtt_port = 1883; //порт`

Подставьте в них адрес и порт используемого вами MQTT брокера.
Также вы можете изменить учетные данные для подключения:

`String mqtt_login="login"; //логин
String mqtt_pass="pass"; //пароль`

Для управления, по умолчанию используется топик: **CatFeeder/cmd/**.
Для отображения статусной информации: **CatFeeder/status/**.
За них отвечают переменные:

`String cmdTopic="CatFeeder/feed/"; //топик управления
String statusTopic="CatFeeder/status/"; //топик статуса`

Тут же вы можете изменить и ID клиента:

`String clientID="CatFeeder2"; //ID клиента`

Также настройка MQTT подключения возможна и через веб интерфейс.
Если все настройки верны, то при успешном подключении к брокеру в статусной панели появится соответствующий значок.

#### Полный список управляющих команд
Команда без параметра включает или отключает функцию. С параметром - устанавливает значение или выполняет действие. 

* **feed** - выдача одной порции корма. (Если указан параметр, то выдать определенное колличество 1-60 гр). Например **feed 40**.
* **info** - получение статусной информации о работе кормушки
* **lastfeed** - время последнего кормления и размер порции
* **temp** - температура и влажность
* **tgbot** - включение/отключение телеграм бота
* **brightlevel** - установить яркость подсветки экрана (параметр 0-255)
* **daytime** - без параметра, включение и отключение снижения яркости экрана. Параметр вида hn:he установка дневного времени. hn-начало, he-конец
* **restart** - перезагрузка устройства

Следующие команды без параметра включают или отключают будильники. С параметром устанавливают его значение и сохраняют в память.
Параметр вида **hh:mm** устанавливает время. Например, **/alarm0 11:20**. Параметр val размер порции в граммах. Например, **/alarm0 40**.
* **alarm0** - Будильник 0
* **alarm1** - Будильник  1
* **alarm2** - Будильник  2
* **alarm3** - Будильник  3

#### Статусные MQTT топики
* **CatFeeder/temp/** - топик температуры с DHT датчика
* **CatFeeder/humid/** - топик влажности с DHT датчика

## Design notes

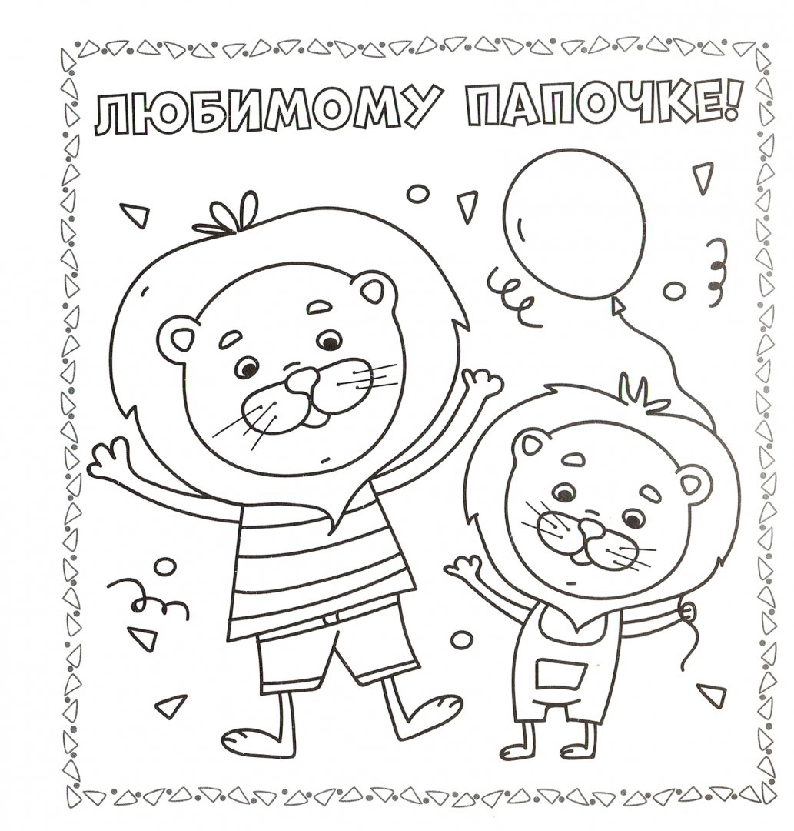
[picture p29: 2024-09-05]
docs/ph_01.png

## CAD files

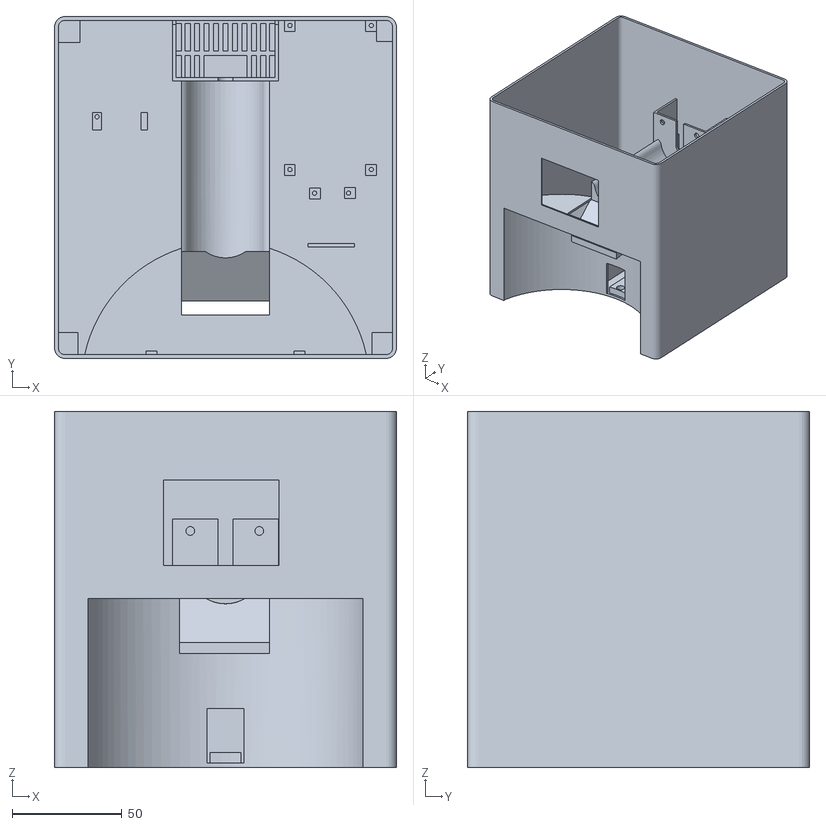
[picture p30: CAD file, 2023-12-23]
3dmodel/корпус.stl
155.5 x 155.5 x 162.0

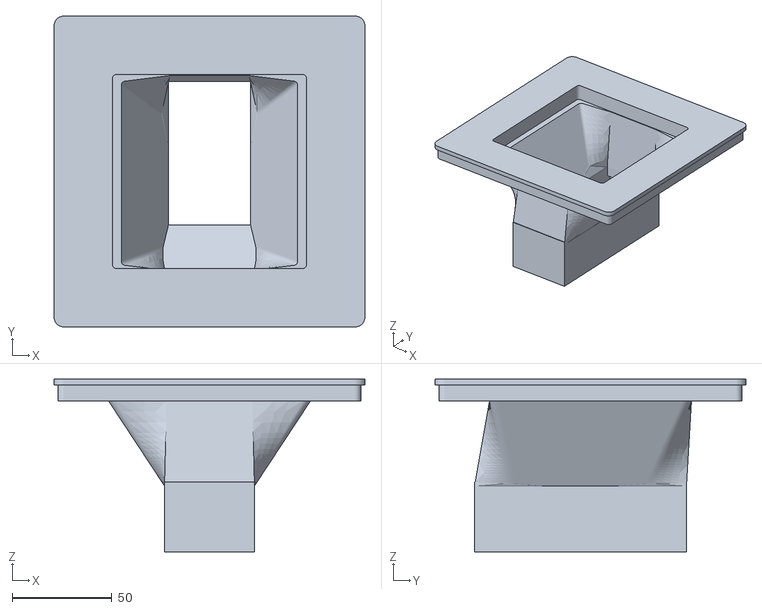
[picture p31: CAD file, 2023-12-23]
3dmodel/крышка.stl
155.5 x 155.5 x 86.5

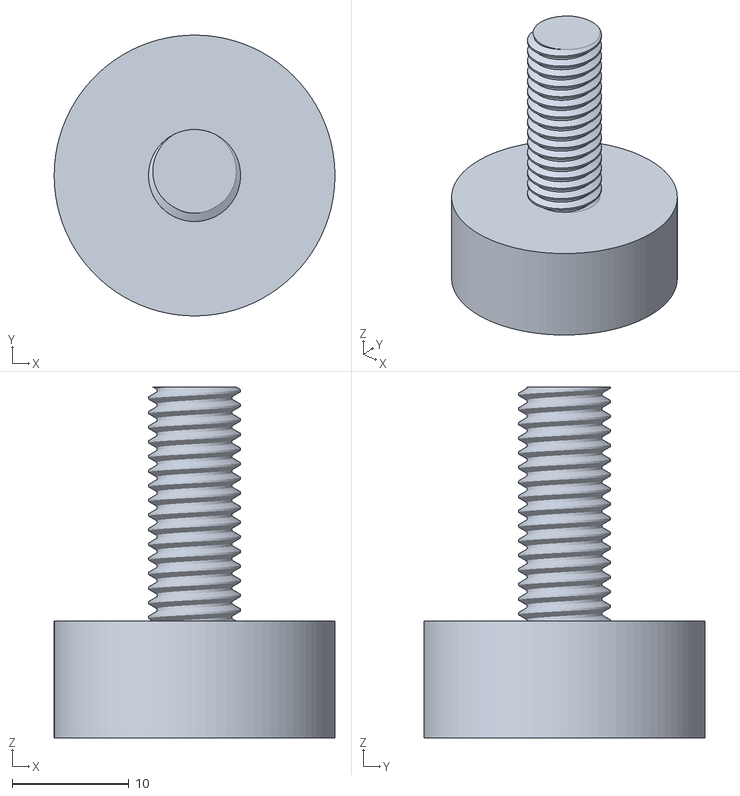
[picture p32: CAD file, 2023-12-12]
3dmodel/Стойках4.stl
24.0 x 24.0 x 30.0

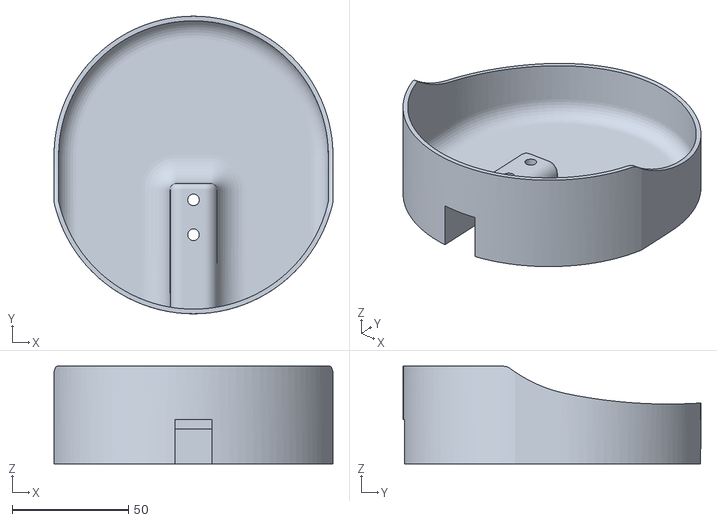
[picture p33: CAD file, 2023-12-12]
3dmodel/миска.stl
120.0 x 128.0 x 42.0

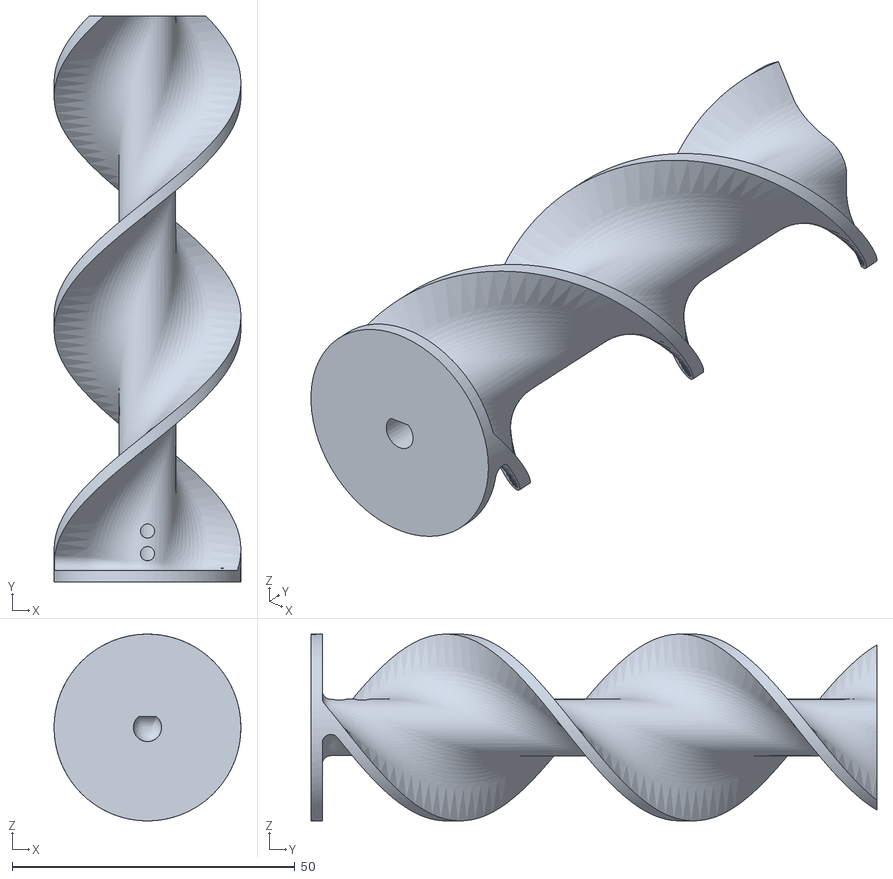
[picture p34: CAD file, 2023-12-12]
3dmodel/шнек.stl
33.0 x 100.0 x 33.0

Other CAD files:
3dmodel/cat_feeder_screw v3.f3d

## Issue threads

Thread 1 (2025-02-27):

отличный проэкт

Alecs2000, 2025-02-27:
хотелось бы очень повторить, но без дисплея , тача, весов и датчика температуры,  на драйвере ILI9341. как бы это корректно выпилить? боюсь что у меня самого мозгов не хватит.

altJSV, 2025-02-28:
https://github.com/AlexGyver/GyverFeed2
За основу был взят этот проект. Правда от него тут осталось только управление серво приводами

Alecs2000, 2025-02-28:
я видел это, но хотелось бы кормушкой рулить из ХА,  через вафлю, в идеале на ESP8266 ESP-01, закупился в свое время.  из железа только драйвер от принтера и мотор.

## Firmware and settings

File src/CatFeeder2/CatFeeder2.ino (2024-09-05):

//Подключение библиотек
#include <lvgl.h> //библиотека пользовательского интерфейса
#include "secrets.h" //различные параметры авторизации
#include <FS.h> //Работа с файловой системой
#include <SPIFFS.h> //файловая система esp32
#include <TFT_eSPI.h> //драйвер дисплея
#include "images.c" //файл с графикой
#include <SPI.h> //драйвер spi
#include <WiFi.h> //библиотека для рабоы с wifi esp32
#include <WiFiManager.h> //Легкая настройка подключения к Wifi сети
#include <GyverNTP.h> //синхронизация с сервером точного времени
#include <GyverTimer.h>//подключение различных таймеров
#include <WiFiClient.h> //работа с wif соединением
#include <PubSubClient.h> //работа по протоколу mqtt
#include <WebServer.h> //веб интерфейс
#include <WiFiUdp.h>//поддержка широковещательных рассылок
#include <ArduinoJson.h>//библиотека для работы с файлами конфигурации
#include <GyverHX711.h> //работа с цифровыми весами
#include <FastBot.h> //Telegram бот
#include <GyverStepper.h> //,библиотека шагового двигателя
#include <Update.h> //OTA обновления
#include <WiFiServer.h> //веб интерфейс и OTA
#include <ESPmDNS.h>//локальный DNS сервер
#include "DHT.h"// библиотека для работы с dht сенсором
#include "webpages.h" //различные скрипты html код

#define TFT_BACKLIGHT 27 //пин подсветки экрана
// Определяем пин и тип датчика температуры DHT22
#define DHT_PIN 14
#define DHT_TYPE DHT22

//добавляем вывод новых символов
#define LV_SYMBOL_SANDCLOCK "\xEF\x82\xB3" //песочные часы
#define LV_SYMBOL_SCALES "\xEF\x82\xB4" //кухонные весы
#define LV_SYMBOL_TIMEOK "\xEF\x82\xB5" //часы ОК
#define LV_SYMBOL_CATFOOD "\xEF\x82\xB6"//кошачья еда
#define LV_SYMBOL_DISPLAY "\xEF\x82\xB7" //монитор
#define LV_SYMBOL_DCLOCK "\xEF\x82\xB8" //цифровые часы
#define LV_SYMBOL_BLUETOOTH "\xEF\x8A\x94" //bluetooth
#define LV_SYMBOL_ASCALES "\xEF\x89\x8E" //аналоговые весы
#define LV_SYMBOL_TELEGRAM "\xEF\x87\x98" //логотип Telegram
#define LV_SYMBOL_WEIGHT "\xEF\x97\x8D" //иконка гири
#define LV_SYMBOL_ACLOCK "\xEF\x80\x97" //аналоговые часы
#define LV_SYMBOL_TEMP "\xEF\x9D\xAB" //иконка температуры
#define LV_SYMBOL_HUMID"\xEF\x9D\xB3" //иконка влажности
#define FILEBUFSIZ 4096
//Выбор типа драйвера
#define STEPDRVTYPE 1 //0-MX1508,  1 - A4988

//файловая система
#define FORMAT_SPIFFS_IF_FAILED true //форматирование файловой системы при ошибке инициализации
#define CALIBRATION_FILE "/TouchCalData" 


//Объявление глобальных переменных и массивов
//массив будильников
uint8_t feedTime[4][4] = {
  {7, 0, 1,20},       // часы, минуты, флаг активности таймера, размер порции
  {12, 0, 1,30},
  {17, 0, 1,30},
  {21, 0, 1,20},
};

uint8_t feedAmountSet = 10; //размер порции на слайдере
uint8_t feedAmount = 10; //размер порции на слайдере
int8_t timezone = 3; //часовой пояс

//Яркость подсветки экрана
uint8_t bright_level=250;
uint8_t daybegin=7; //начало дня
uint8_t dayend=22; //конец дня
bool daytime=true; //отключение подсветки в ночное время

//переключатель цветовой темы оформления
bool theme = true;  //true темная тема, false светлая

//включение телеграм бота
bool tg_bot = true;

//флаг выполнения перезагрузки
bool espRes=false;

uint16_t lastFeed=0; //время последнего кормления

long tareWeight=0; //вес миски в граммах
long foodWeight=0; //вес еды в миске
float scales_param=191.7; //коэффициент взвешивания
uint16_t scales_control_weight=30;

//Параметры шагового двигателя
uint8_t fwd_steps=60; //шагов вперед
uint8_t bck_steps=20; //шагов назад
float step_speed = 100; //скорость вращения
uint8_t max_revs=16; //максимальное число оборотов до остановки мотора

//Температура и влажность
float temperature;
float humidity;
float temp_cal=25.0; //температура калибровки тензодатчика

String logStr = "Старт сессии:\n"; //лог действий в веб интерфейсе
char tempBuf[256]; //буфер для работы с файлами
File fsUploadFile; //буфер загрузки файла
bool fsFound = false; //флаг того что ФС найдена

void fsList(void);
bool initFS(bool format, bool force);

//Параметры экрана
static const uint16_t screenWidth = 320; //ширина экрана
static const uint16_t screenHeight = 240; //высота экрана


//MQTT настройки
bool usemqtt = true;
long lastReconnectAttempt = 0;

//Иконки статуса
String status_icons=LV_SYMBOL_WIFI;

//Файл конфигурации
const char * filename = "/config.json";  // имя файла конфигурации

//Объявление служебных переменных для LVGL
static lv_disp_draw_buf_t draw_buf;
static lv_color_t buf[screenWidth * screenHeight / 6];

//объекты интерфейса LVGL
    //Контейнеры
    static lv_obj_t * ui_feedwindow; // окно кормления
    static lv_obj_t * ui_stepwindow; //окно настроек шаговика
    static lv_obj_t * ui_scaleswindow; //окно настроек шаговика 
    static lv_obj_t * ui_tabview; // панель вкладок
    static lv_obj_t * ui_tabview_settings; //панель вкладок настроек
    //Панель состояния
    static lv_obj_t * ui_status_icons; //статус wifi
    static lv_obj_t * ui_status_ip; //ip адрес
    //Экранная клавиатура
    static lv_obj_t * kb; //клавиатура
    //Экранные объекты
      //Основной экран
      //Вкладка кормления
      static lv_obj_t * ui_clock; //часы
      static lv_obj_t * ui_label_feedAmount; //размер порции
      static lv_obj_t * ui_remain; //осталось времени до выдачи порции
      static lv_obj_t * ui_food_weight; //вес порции в миске
      static lv_obj_t * ui_temp_label; //температура
      static lv_obj_t * ui_humid_label; //влажность
      static lv_obj_t * ui_slider_feed_amount;//слайдер размера порции
       //Вкладка таймеры
      static lv_obj_t * ui_timer1_hour; //слайдер часов будильника 1
      static lv_obj_t * ui_timer1_minute; //слайдер минут будильника 1
      static lv_obj_t * ui_timer1_check; //активатор будильника 1
      static lv_obj_t * ui_timer1_amount;//размер порции будильника 1
      static lv_obj_t * ui_timer2_hour; //слайдер часов будильника 2
      static lv_obj_t * ui_timer2_minute; //слайдер минут будильника 2
      static lv_obj_t * ui_timer2_check; //активатор будильника 2
      static lv_obj_t * ui_timer2_amount;//размер порции будильника 2
      static lv_obj_t * ui_timer3_hour; //слайдер часов будильника 3
      static lv_obj_t * ui_timer3_minute; //слайдер минут будильника 3
      static lv_obj_t * ui_timer3_check; //активатор будильника 3
      static lv_obj_t * ui_timer3_amount;//размер порции будильника 3
      static lv_obj_t * ui_timer4_hour; //слайдер часов будильника 4
      static lv_obj_t * ui_timer4_minute; //слайдер минут будильника 4
      static lv_obj_t * ui_timer4_check; //активатор будильника 4
      static lv_obj_t * ui_timer4_amount;//размер порции будильника 4


      //Окно кормления
      static lv_obj_t * ui_feed_progress_bar; //полоса прогресса кормления
      static lv_obj_t * ui_feed_progress_bar_label; //текст на полосе прогресса кормления
      static lv_obj_t * ui_feed_label_max; //целевое значение корма
      static lv_obj_t * ui_feed_label_cur; //текущее значение корма
      


      //Окно настроек
      static lv_obj_t * ui_set_panel_display_bright_slider; //слайдер изменения ярккости подсветки экрана
      static lv_obj_t * ui_backlight_slider_label; //текст на слайдере яркости подсветки экрана
      static lv_obj_t * slider_daytime_label; //текст на слайдере подсветки в ночное время
      static lv_obj_t * ui_set_display_daytime_switch; //переключатель подсветки в ночное время
      static lv_obj_t * ui_slider_day_time; //слайдер установки дневного времени
      static lv_obj_t * ui_gmt_slider_label; //текст на слайдере изменения часового пояса
      static lv_obj_t * ui_set_panel_usemqtt_switch; //переключатель mqtt
      static lv_obj_t * ui_set_panel_mqtt_adress_ta; //адрес mqtt
      static lv_obj_t * ui_set_panel_mqtt_port_ta; //порт mqtt
      static lv_obj_t * ui_set_panel_mqtt_login_ta; //логин mqtt
      static lv_obj_t * ui_set_panel_mqtt_pass_ta; //пароль mqtt
      static lv_obj_t * ui_set_panel_mqtt_control_ta; //топик управления mqtt
      static lv_obj_t * ui_set_panel_mqtt_status_ta; //топик статуса mqtt
      static lv_obj_t * ui_set_panel_telegram_token_ta; //токен телеграм бота
      static lv_obj_t * ui_set_panel_telegram_chatid_ta; //чат ID телеграм бота
      static lv_obj_t * ui_set_panel_telegram_bot_switch;//переключатель бота
      static lv_obj_t * ui_set_panel_scales_coef_label; //коэффициент весов

      //Окно настроек шагового двигателя
      static lv_obj_t * ui_step_window_fwdstep_slider_label;//надаись на слайдере шагов вперед
      static lv_obj_t * ui_step_window_bckstep_slider_label;//надаись на слайдере шагов назад
      static lv_obj_t * ui_step_window_speed_slider_label;//надаись на слайдере скорость вращения
      static lv_obj_t * ui_step_window_maxrev_slider_label;//максимум оборотов до остановки


      //Окно калибровки весов
      static lv_obj_t * ui_scales_window_param_label; //калибровочный коэффициент
      static lv_obj_t * ui_scales_window_weight; //спинбокс калибровочного веса

//Инициализация библиотек
GyverNTP ntp(timezone); //инициализация работы с ntp, в параметрах часовой пояс
TFT_eSPI tft = TFT_eSPI(); // создаем экземпляр объекта TFT_eSPI
WiFiManager wm; //экземпляр объекта wifi manager
WiFiClient esp32Client; //обмен данными по wifi
PubSubClient client(esp32Client); //инициализируем библиотеку mqtt
WebServer server(80); //поднимаем веб сервер на 80 порту
GyverHX711 sensor(16, 13, HX_GAIN64_A); //data,clock, коэффициент усиления
FastBot bot (bot_token); //инициализация библиотеки ТГ бота
DHT dht(DHT_PIN, DHT_TYPE); // Датчик DHT

//Инициализируем библиотеку шагового двигателяв зависимости от типа драйвера
#if (STEPDRVTYPE==1)
GStepper<STEPPER2WIRE> stepper(200, 32,33,25); //шагов на полный оборот двигателя, step, dir, en (смотреть схему в документации)
#else
GStepper<STEPPER4WIRE> stepper(200, 26,25,32,33); //шагов на полный оборот двигателя, фаза 1, фаза 2, фаза 3, фаза 4 (смотреть схему в документации)
#endif

//Инициализация таймеров
GTimer reftime(MS);//часы
GTimer reftemp(MS);//взвешивание миски
GTimer reflvgl(MS); //обновление экранов LVGL 
GTimer refremain(MS); //таймер обновления времени до кормления 
GTimer reffeedtime(MS); //таймер времени до запуска кормления
GTimer refchecktime(MS);//проверка срабатывания таймеров кормления
GTimer refsaveconfigdelay(MS);//проверка срабатывания таймеров кормления 

/***** БЛОК СЛУЖЕБНЫХ ФУНКЦИЙ ****/
//Функция для вывода содержимого буфера экрана на дисплей
void my_disp_flush( lv_disp_drv_t *disp, const lv_area_t *area, lv_color_t *color_p )
  {
 uint32_t w = ( area->x2 - area->x1 + 1 );
 uint32_t h = ( area->y2 - area->y1 + 1 );

 tft.startWrite();
 tft.setAddrWindow( area->x1, area->y1, w, h );
 tft.pushColors( ( uint16_t * )&color_p->full, w * h, true );
 tft.endWrite();

 lv_disp_flush_ready( disp );
  }

// Вычисление координат касания
void my_touchpad_read( lv_indev_drv_t * indev_driver, lv_indev_data_t * data )
{
    uint16_t touchX, touchY;

    bool touched = tft.getTouch( &touchX, &touchY, 600 );

    if( !touched )
    {
        data->state = LV_INDEV_STATE_REL;
    }
    else
    {
        data->state = LV_INDEV_STATE_PR;
        data->point.x = touchX;
        data->point.y = touchY;
    }
}

//калибровка тач скрина
void touch_calibrate(bool rewrite)
{
  uint16_t calData[5];
  uint8_t calDataOK = 0;

  if (rewrite) {SPIFFS.remove(CALIBRATION_FILE); rewrite=false;}
  // Проверка наличия файла калибровки и его целостности
  if (SPIFFS.exists(CALIBRATION_FILE)) {
      File f = SPIFFS.open(CALIBRATION_FILE, "r");
      if (f) {
        if (f.readBytes((char *)calData, 14) == 14)
          calDataOK = 1;
        f.close();
      }
    
  }

  if (calDataOK && !rewrite) {
    // настройки калибровки верны
    tft.setTouch(calData);
  } else {
    // выводим интерфейс калибровки экрана
    tft.fillScreen(TFT_BLACK);
    tft.setCursor(20, 0);
    tft.setTextSize(1);
    tft.setTextColor(TFT_WHITE, TFT_BLACK);

    tft.println("Touch a points to calibrate...");
    tft.println();


    tft.calibrateTouch(calData, TFT_MAGENTA, TFT_BLACK, 15);
    tft.setTextColor(TFT_GREEN, TFT_BLACK);
    tft.println("Screen calibration complete!");

    // сохраняем данные
    File f = SPIFFS.open(CALIBRATION_FILE, "w");
    if (f) {
      f.write((const unsigned char *)calData, 14);
      f.close();
      ESP.restart();//перезагрузка esp32
    }
  }
}

/***** КОНЕЦ БЛОКА СЛУЖЕБНЫХ ФУНКЦИЙ ****/

void setup() 
{
  Serial.begin( 115200 ); //открытие серийного порта
  stepper.setRunMode(FOLLOW_POS);//устанвливаем режим работы двигателя Следовать к позиции
  stepper.setAcceleration(0);//отключаем ускорения двигателя
  //Настройки экрана  
  tft.init(); // инициализируем дисплей
  tft.setRotation (1); //ориентация эрана горизонтальная
  lastReconnectAttempt = 0; //таймер mqtt
  //Инициализация файловой системы
 if (fs_init())
  {
        Serial.println("Чтение файла конфигурации...");
        logStr+="Чтение файла конфигурации...";
        loadConfiguration("/config.json"); 
        readFile(SPIFFS, "/config.json");
        touch_calibrate(false);
  }
  logStr+="Запуск интерфейса... ";

  lv_init();//инициализация LVGL
  //Далее идут функции настройки LVGL 
  lv_disp_draw_buf_init( &draw_buf, buf, NULL, screenWidth * screenHeight / 6 ); //создаем буфер для вывода информации на экран
 
  //далее идет настройка параметров экрана
  static lv_disp_drv_t disp_drv; //объявляем переменную для хранения драйвера дисплея
  lv_disp_drv_init( &disp_drv ); //базовая инициализация драйвера
  disp_drv.hor_res = screenWidth; //ширина экрана
  disp_drv.ver_res = screenHeight; //высота экрана
  disp_drv.flush_cb = my_disp_flush; //функция которая выводит содержимое буфера в заданное место экрана. Указываем имя функции которую мы написали выше
  disp_drv.draw_buf = &draw_buf; //объявляем библиотеке, что содержимое буфера экрана находится в переменной draw_buf
  lv_disp_drv_register( &disp_drv ); //регистрируем драйвер дисплея и сохраняем его настройки
  
  // Инициализируем драйвер тачскрина
  static lv_indev_drv_t indev_drv; //объявляем переменные для хранения драйвера тачскрина
  lv_indev_drv_init( &indev_drv ); // базовая инициализация драйвера
  indev_drv.type = LV_INDEV_TYPE_POINTER; //указываем тип драйвера. В данном случае это тачскрин
  indev_drv.read_cb = my_touchpad_read; //указываем имя функции обработчика нажатий на тачскрин, которую мы создали
  lv_indev_drv_register( &indev_drv ); //регистрация драйвера тачскрина и сохранение его настроек
  
  
//Отрисовка интерфейса
  draw_interface();
  logStr+="Ок...\n";
 
 //Инициализация wifi
 logStr+="Инициализация WiFi...\n";
  WiFi.mode(WIFI_AP_STA);
  WiFi.onEvent(WiFiGotIP, WiFiEvent_t::ARDUINO_EVENT_WIFI_STA_GOT_IP);
  if(!wm.autoConnect("CatFeeder2","12345678")) {
        Serial.println("Не удалось подключиться к сети");
        logStr+="Не удалось подключиться к сети...\n";
        lv_obj_add_flag(ui_status_icons, LV_OBJ_FLAG_HIDDEN); 
        lv_obj_add_flag(ui_status_ip, LV_OBJ_FLAG_HIDDEN); 
    } 
    else {  
        Serial.println("Подключение успешно");
        lv_obj_clear_flag(ui_status_icons, LV_OBJ_FLAG_HIDDEN); //Отображение иконки wifi
        lv_obj_clear_flag(ui_status_ip, LV_OBJ_FLAG_HIDDEN); //Показать IP адрес
        ntp.begin(); //сервис синхронизации времени
       
        //подключаем Telegram бота
        logStr+="Телеграм бот инициализация... ";
        bot.setChatID(chatID); // открываем чат
        bot.attach(newMsg); //подключаем функцию обработки сообщений
        bot.sendMessage("Cat Feeder 2 готов к работе!"); //отправляем сообщение о готовности
        logStr+="Ок\n";
    } 
  
  //запуск сервисов
  // DNS
  if (!MDNS.begin("catfeeder2")) {Serial.println("Ошибка открытия MDNS!");logStr+="Ошибка открытия MDNS!\n";}   
  else
    Serial.println("mDNS запущен. имя хоста = http://catfeeder2.local");
    logStr+="mDNS запущен. имя хоста = http://catfeeder2.local\n";
  server_init();//запуск веб сервера
  
  //Запуск сервиса DHT
  pinMode(DHT_PIN, INPUT);
  logStr+="Запуск DHT... ";
  Serial.println("Запуск DHT...");
  dht.begin();
  logStr+="Ок\n";

  logStr+="Запуск Таймеров... ";
  
  //Установка значений таймеров
  reftime.setInterval(1000);//обновление времени на экране 1000 мс или 1 секунда
  refremain.setInterval(10000);//обновление времени на экране 30000 мс или 30 секунд
  reflvgl.setInterval(30);//обновление экрана LVGL 30 мс
  refchecktime.setInterval(500);//раз в полсекунды
  reftemp.setInterval(10000);//взвешивание миски разв 10 секунд
  refsaveconfigdelay.stop();
  logStr+="Ок\n";
  logStr+="Настройка подсветки экрана... ";
  pinMode(TFT_BACKLIGHT,OUTPUT);//Переключаем пин подсветки на передачу данных
  analogWrite(TFT_BACKLIGHT,bright_level);
  logStr+="Ок\n";
  logStr+="Устройство готово к работе\n";
  }

/**** ВТОРОЙ БЛОК ФУНКЦИЙ ****/

//Подключение к Wifi успешно. Получен ip адрес
void WiFiGotIP(WiFiEvent_t event, WiFiEventInfo_t info){
  Serial.println("WiFi подключен");
  logStr +="WiFi подключен. IP: ";
  IPAddress ip = WiFi.localIP();
  String ipString =String(ip[0]);
  for (byte octet = 1; octet < 4; ++octet) {
    ipString += '.' + String(ip[octet]);
  }
  lv_label_set_text(ui_status_ip,ipString.c_str());
  Serial.println("IP address: ");
  logStr+=ipString;
  logStr+="\n";
  Serial.println(ip);
  if (usemqtt) MQTT_init();//Подключение к MQTT брокеру
  
}
/**** КОНЕЦ БЛОКА ФУНКЦИЙ ****/


void loop() 
{
  //Проверка статуса wifi
  if (WiFi.status() == WL_CONNECTED)
    { 
      status_icons="";
      if (tg_bot) status_icons+=LV_SYMBOL_TELEGRAM" ";
      if (client.connected()) 
      {
        status_icons+=LV_SYMBOL_LOOP" ";
      }
      else
      {
        long now = millis();
      if (now - lastReconnectAttempt > 5000) 
        {
          lastReconnectAttempt = now;
          if (client.connect(clientID.c_str(), mqtt_login.c_str(),mqtt_pass.c_str(),statusTopic.c_str(),1,true,"Клиент отключен"))
            {
              client.subscribe(cmdTopic.c_str());
              lastReconnectAttempt = 0;
            }
        }
      }  
      status_icons+=LV_SYMBOL_WIFI;
      lv_label_set_text(ui_status_icons, status_icons.c_str());
      lv_obj_clear_flag(ui_status_icons, LV_OBJ_FLAG_HIDDEN);
      lv_obj_clear_flag(ui_status_ip, LV_OBJ_FLAG_HIDDEN);
      ntp.tick(); //синхронизируем время
      if (ntp.synced() && lastFeed==0) lastFeed=ntp.hour()*60 + ntp.minute(); //заполняем время последнего кормления при первом запуске. По умолчанию ставим время первой синхронизации с с ервером времени
    }
  else
    {
      lv_obj_add_flag(ui_status_icons, LV_OBJ_FLAG_HIDDEN);
      lv_obj_add_flag(ui_status_ip, LV_OBJ_FLAG_HIDDEN);
    }
  
  //Проверяем значения таймеров
  if (reflvgl.isReady()) { lv_timer_handler();} //Обновляем экран
  if (reftime.isReady()) {if (lv_tabview_get_tab_act(ui_tabview)==0) {lv_label_set_text(ui_clock, ntp.timeString().c_str());}} //обновляем занчение часов на экране
  if (refremain.isReady()){feedRemain();} //Отображение времени оставшегося до кормления
  if (reffeedtime.isReady()) {reffeedtime.stop();feed(feedAmount);}//ожидание загрузки экрана кормления и запуск функции
  //Измерение температуры
  if (reftemp.isReady()) 
    {
      temperature = dht.readTemperature();
      lv_label_set_text_fmt(ui_temp_label, LV_SYMBOL_TEMP" %.1f °С",temperature);
      humidity = dht.readHumidity();
      lv_label_set_text_fmt(ui_humid_label, LV_SYMBOL_HUMID" %.1f%%",humidity);
      if (usemqtt)
      {
      String mqtemp=String (temperature);
      String mqhumid=String (humidity);
      client.publish(tempTopic.c_str(),mqtemp.c_str());
      client.publish(humidTopic.c_str(),mqhumid.c_str());
      }
    }
  if (refsaveconfigdelay.isReady()) {refsaveconfigdelay.stop();logStr+="Сохранение настроек..."; saveConfiguration("/config.json") ;} //сохраняем настройки
  if (refchecktime.isReady()) //проверка таймера кормления
      {
        static byte prevMin = 0;
          if (ntp.status()==0)
            {
              if (prevMin != ntp.minute()) 
                {//исключаем двойной запуск кормления при срабатывании таймера
                  prevMin = ntp.minute();
                  for (byte i = 0; i < sizeof(feedTime) / 2; i++)    // проверяем массив с расписанием
                  if (feedTime[i][0] == ntp.hour() && feedTime[i][1] == ntp.minute() &&feedTime[i][2] == 1) prefid(feedTime[i][3]);
                  //проверка включен ли ночной режим
                  if (daytime) 
                  {
                    if (ntp.hour()>=daybegin && ntp.hour()<dayend) {analogWrite(TFT_BACKLIGHT,bright_level);} else {analogWrite(TFT_BACKLIGHT,20);} 
                  } else {analogWrite(TFT_BACKLIGHT,bright_level);}
                  
                }
            }
  }
  if (usemqtt) client.loop(); //чтение состояния топиков MQQT
  if (tg_bot) bot.tick(); //поддерживаем соединение с telegram ботом
  server.handleClient(); //обработка запросов web интерфейса
  if (espRes)
    {
      bot.tickManual();
      ESP.restart();
    }
}

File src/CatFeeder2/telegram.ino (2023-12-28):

/*
Все для работы Телеграм бота
*/
//Обработчик команд telegram бота
void newMsg(FB_msg& msg) 
{
  String param;//параметр
  String command;//команда
  uint8_t val,val2; //вспомогательные значения
  
  int8_t paramstart=msg.text.indexOf(" "); //ищем символ пробела
  if (paramstart>0) {command=msg.text.substring(0,paramstart); param=msg.text.substring(paramstart+1);} else {command=msg.text;} //если есть параметры записываем их в строку param
  if (command=="/feed") {//выдать корм
                          if (paramstart>0) //если был указан параметр
                              {
                              val=param.toInt();
                              if (val>0 && val<=60) prefid(val); else {bot.sendMessage("Укажите значение в интервале от 1 до 60!");} //при корректном значении параметра выдаем установленное значение корма
                              } else {prefid(feedAmountSet);} //выдаем заранее установленное значение корма
                              
                        } 
  if (command=="/brightlevel") {//установить яркость подсветки
                          if (paramstart>0) //если был указан параметр
                              {
                              val=param.toInt();
                              if (val>0 && val<=255) {bright_level=val; lv_slider_set_value(ui_set_panel_display_bright_slider, bright_level, LV_ANIM_OFF); lv_label_set_text_fmt(ui_backlight_slider_label, "%d%", (int)lv_slider_get_value(ui_set_panel_display_bright_slider));} 
                              else {bot.sendMessage("Укажите значение в интервале от 1 до 255!");} //при коректном значении устанавливаем яркость подсветки
                              } else bot.sendMessage("Укажите в качестве параметра значение от 1 до 255!");; //выдаем предупреждение в чат
                        }
  if (command=="/daytime") {//отключение подсветки экрана в ночное время
                          if (paramstart>0) //если был указан параметр
                              {
                              int8_t paramtype=param.indexOf(":");
                              if (paramtype>0)
                                {
                                  val=param.substring(0,paramtype).toInt();
                                  val2=param.substring(paramtype+1).toInt();
                                  if (val>=0 && val2>=0 && val<24 && val2<24 && val<val2)
                                    {
                                      daybegin=val;//начало дня
                                      dayend=val2;//конец дня
                                      lv_slider_set_left_value(ui_slider_day_time, daybegin, LV_ANIM_OFF);
                                      lv_slider_set_value(ui_slider_day_time, dayend, LV_ANIM_OFF);
                                      bot.sendMessage("Интервал дневного время установлен: с "+String(daybegin)+" до "+String(dayend)+" часов"); refsaveconfigdelay.setInterval(10000);
                                    } else {bot.sendMessage("Неверные параметры команды");} 
                              } else {
                                daytime=!daytime;
                                if (daytime) {bot.sendMessage("Отключение подсветки экрана ночью включено"); lv_obj_add_state(ui_set_display_daytime_switch, LV_STATE_CHECKED);} else {bot.sendMessage("Отключение подсветки экрана ночью выключено");lv_obj_clear_state(ui_set_display_daytime_switch, LV_STATE_CHECKED);} refsaveconfigdelay.setInterval(10000);} 
                              }
                        }  
  if (command=="/info") {tg_send_info();} //информация о системе
  if (command=="/mqtt") {usemqtt=!usemqtt; if (usemqtt) {bot.sendMessage("MQTT включен");lv_obj_add_state(ui_set_panel_usemqtt_switch, LV_STATE_CHECKED);} else {bot.sendMessage("MQTT отключен");lv_obj_clear_state(ui_set_panel_usemqtt_switch, LV_STATE_CHECKED);} refsaveconfigdelay.setInterval(10000);} //Включаем и отключаем mqtt
  if (command=="/lastfeed") {bot.sendMessage("Время последнего кормления: "+ String((uint16_t)lastFeed/60)+":"+String((uint8_t)lastFeed%60)+" Размер порции: "+String(feedAmount)+ " грамм");}
  if (command=="/temp") {bot.sendMessage("Температура: "+ String(temperature)+"°С Влажность: "+String(humidity)+"%");}
  if (command=="/commandlist") {tg_send_cmdhelp();}
  if (command=="/restart") {espRes=true;}//перезагрузка устройства
  //Установка значений таймеров
  if (paramstart>0) //если был указан параметр
    {
      int8_t paramtype=param.indexOf(":");
      if (paramtype>0)
        {
          val=param.substring(0,paramtype).toInt();
          val2=param.substring(paramtype+1).toInt();
          if (val>=0 && val2>=0 && val<24 && val2<60)
          {
            if (command=="/alarm0") {feedTime[0][0]=val; feedTime[0][1]=val2; bot.sendMessage("Будильник 0 установлен на: "+String(feedTime[0][0])+":"+String(feedTime[0][1])); lv_roller_set_selected(ui_timer1_hour, feedTime[0][0], LV_ANIM_OFF); lv_roller_set_selected(ui_timer1_minute, feedTime[0][1], LV_ANIM_OFF); refsaveconfigdelay.setInterval(10000);}
            if (command=="/alarm1") {feedTime[1][0]=val; feedTime[1][1]=val2; bot.sendMessage("Будильник 1 установлен на: "+String(feedTime[1][0])+":"+String(feedTime[1][1])); lv_roller_set_selected(ui_timer2_hour, feedTime[1][0], LV_ANIM_OFF); lv_roller_set_selected(ui_timer2_minute, feedTime[1][1], LV_ANIM_OFF); refsaveconfigdelay.setInterval(10000);}
            if (command=="/alarm2") {feedTime[2][0]=val; feedTime[2][1]=val2; bot.sendMessage("Будильник 2 установлен на: "+String(feedTime[2][0])+":"+String(feedTime[2][1])); lv_roller_set_selected(ui_timer3_hour, feedTime[2][0], LV_ANIM_OFF); lv_roller_set_selected(ui_timer3_minute, feedTime[2][1], LV_ANIM_OFF); refsaveconfigdelay.setInterval(10000);}
            if (command=="/alarm3") {feedTime[3][0]=val; feedTime[3][1]=val2; bot.sendMessage("Будильник 3 установлен на: "+String(feedTime[3][0])+":"+String(feedTime[3][1])); lv_roller_set_selected(ui_timer4_hour, feedTime[3][0], LV_ANIM_OFF); lv_roller_set_selected(ui_timer4_minute, feedTime[3][1], LV_ANIM_OFF); refsaveconfigdelay.setInterval(10000);}
          } else {bot.sendMessage("Установите значение в пределах 0:00 - 23:59!");}  
        }
        else
        {
          val = param.toInt(); 
          if (val>1 && val<=60)
          {
          if (command=="/alarm0") {feedTime[0][3]=val; bot.sendMessage("Количество корма будильника 0 установлено на: "+String(feedTime[0][3])+" грамм"); lv_spinbox_set_value(ui_timer1_amount,feedTime[0][3]); refsaveconfigdelay.setInterval(10000);}
          if (command=="/alarm1") {feedTime[1][3]=val; bot.sendMessage("Количество корма будильника 1 установлено на: "+String(feedTime[1][3])+" грамм"); lv_spinbox_set_value(ui_timer2_amount,feedTime[1][3]); refsaveconfigdelay.setInterval(10000);}
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

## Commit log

2023-10-27 Первый релиз
2023-10-29 Добавлена поддержка дисплея
2023-10-29 Добавлена поддержка LVGL и сенсорного экрана
2023-10-29 Вертикальная ориентация экрана, отладка сенсорного экрана
2023-10-29 Добавлен менеджер wifi. Оптимизация кода
2023-10-29 Чистка кода. Создание интерфейса вкладок и строки состояния
2023-10-29 Настройка размера порции и кнопка выдачи корма
2023-10-29 Добавлено описание проекта
2023-10-30 Правки шрифтов и интерфейса. Добавлена настройка таймеров
2023-10-31 Вывод окна состояния при нажатии на кнопку покормить
2023-10-31 Добавлена работа по протоколу MQTT
2023-11-01 Добавлена анимация оставшегося времени до кормления. Реализован запуск кормушки по таймерам
2023-11-01 Обновлено описание проекта
2023-11-01 Починка индикатора времени до следующей кормежки
2023-11-02 Функция управления таймерами. Изменен экран выдачи пищи
2023-11-02 Добавлен веб интерфейс
2023-11-02 Перенос параметров авторизации в отдельный файл
2023-11-02 Добавлен интерфейс работы с файловой системой и файлами конфигурации
2023-11-02 Добавлено сохранение и запись настроек в файл конфигурации
2023-11-04 Добавлен экран настроек
2023-11-04 Переключение темы оформления
2023-11-05 Добавлена информация по распиновке платы
2023-11-05 Отключен пин прерывания в драйвере тач скрина
2023-11-05 Управление подсветкой экрана
2023-11-05 Полностью переписан драйвер тачскрина. Добавлен экран калибровки тача
2023-11-06 Удалена настройка яркости экрана. Добавлена кнопка вызова калибровки сенсора в настройки
2023-11-06 Обновлена документация к проекту
2023-11-06 Добавлены OTA обновления
2023-11-17 Ориентация экрана изменена на альбомную
2023-11-17 Изменен интерфейс
2023-11-18 Чистка памяти от неиспользуемых ресурсов
2023-11-18 Вкладки на экране настроек
2023-11-18 Настройка визуального стиля веб интерфейса
2023-11-25 Дополнена документация к проекту
2023-11-25 Добавлена поддержка цифровых весов
2023-11-25 Управление подсветкой
2023-11-25 Настройка размера порции для каждого из таймеров
2023-11-26 Правка интерфейса. Добавлена работа через Telegram бота
2023-11-26 Настройки Telegram бота в меню
2023-11-27 Добавлен экран калибровки цифровых весов
2023-11-27 Обновлена документация
2023-11-27 Исправлены ошибки отображения интерфейса
    [CatFeeder2.ino, interface.ino]
2023-11-28 Добавлены настройки MQTT
2023-11-29 Переход на библиотеку GyverStepper для управления шаговыми двигателями
2023-11-29 Обновление документации
2023-11-29 Добавлено окно настройки шагового двигателя
2023-11-30 Активированы настройки шагового двигателя
2023-11-30 Дописан функционал цифровых весов
2023-12-01 Значительные правки веб интерфейса
2023-12-02 Настройка стилей веб интерфейса. Правка багов
2023-12-02 Дополнена документация
2023-12-02 Добавлены новые команды Telegram бота
2023-12-03 Исправлен баг с сохранением настроек в веб-интерфейсе
    [webserver.ino]
2023-12-03 Обновление лицензионного соглашения
2023-12-03 Исправлены ответы веб сервера
    [webserver.ino]
2023-12-04 Поддержка протокола SSDP
2023-12-07 Убрана поддержка SSDP
2023-12-08 Переписано OTA обновление и добавлен файловый менеджер
2023-12-11 Полностью переписаны функции работы с цифровыми весами
2023-12-11 Датчик DHT22, корректировка весов в зависимости от температуры
2023-12-12 Добавлен mDNS, правки интерфейса
2023-12-12 Добавлены модели для 3Д печати
    [Стойках4.stl, корпус.stl, миска.stl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]
2023-12-12 Добавлена выдача корма по весу
    [крышка.stl]
2023-12-12 Оптимизация веб интерфейса
2023-12-13 Уменьшены значения выдаваемого корма
2023-12-13 Исправлена модель крышки
    [крышка.stl]
2023-12-19 Изменение способа подключения шагового двигателя
2023-12-19 Настройки будильников в веб интерфейсе
2023-12-20 Добавлена информация о температуре и влажности в веб интерфейс
2023-12-20 Незначительные правки интерфейса веб сервера
2023-12-20 Фикс багов веб интерфейса
2023-12-20 Обновлены иконка. Фикс багов
2023-12-20 Лог работы в веб интерфейсе
2023-12-20 Команды Telegaram бота. OTA обновление
2023-12-22 Доработан функционал телеграм бота
2023-12-22 Доработан функционал MQTT
2023-12-22 Глобальная чистка кода
2023-12-22 Чистка репозитория
2023-12-23 Добавлена команда перезагрузки
2023-12-23 Исправлены модели
    [cat_feeder_screw v3.f3d, корпус.stl, крышка.stl]
2023-12-26 Добавлены настройки яркости экрана
2023-12-28 Исправлен вывод интерфейса
2023-12-28 Исправление яркости подсветки. Статус во время кормления
    [CatFeeder2.ino, feedFunc.ino, telegram.ino]
2023-12-28 Добавлена защита двигателя при некорректных показаниях весов
2023-12-31 Добавлена настройка отключения двигателя при достижении максимума оборотов
2023-12-31 Исправление изменения яркости подсветки через веб интерфейс
    [filesystem.ino, webserver.ino]
2024-09-05 Публикация температуры, влажности и времени кормления в mqtt топики
2024-09-05 Исправление документации
2024-09-05 Добавлено автоматическое восстановление подключения к MQTT брокеру
